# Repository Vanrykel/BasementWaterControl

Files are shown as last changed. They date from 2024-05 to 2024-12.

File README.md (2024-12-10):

# Basement Water Control

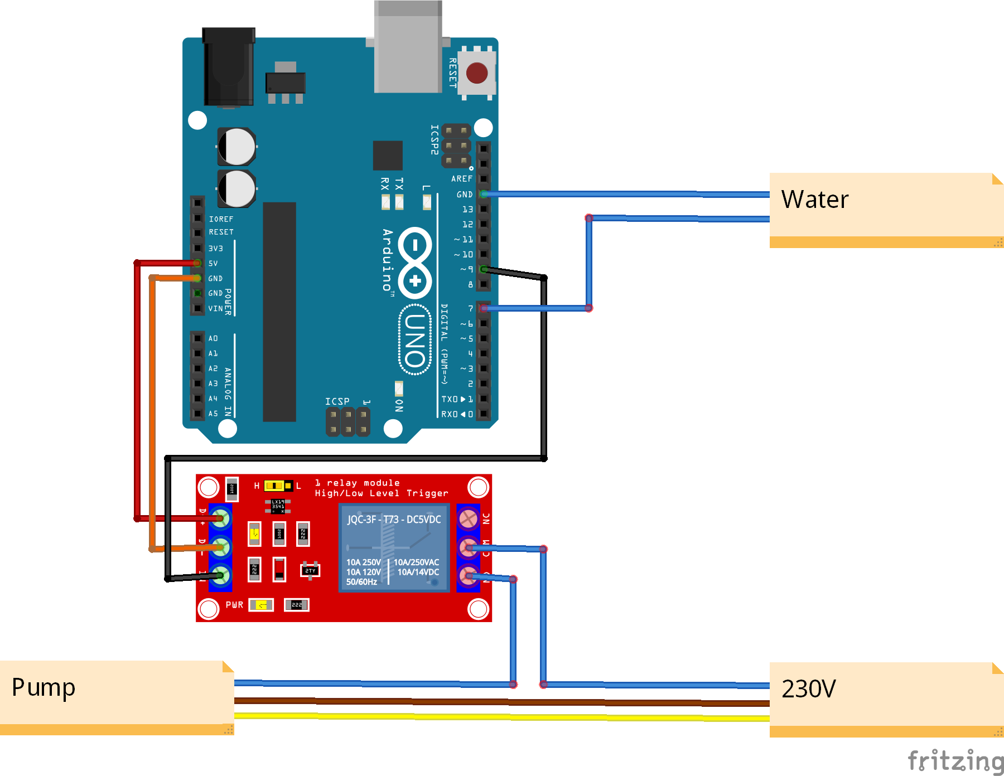
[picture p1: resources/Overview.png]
Overview


## About the project

The basement was consistently flooded with groundwater. To address this issue, a hole has been made in the floor to collect the water, which is then pumped out using a submersible pump. However, due to the shallow depth of the hole, the pump's float switch cannot function effectively. To address this issue, an Arduino is used to detect when the hole in the floor is filled with water. Upon detection, the Arduino will activate a relay to power the submersible pump. The float switch of the pump will be fixed to ensure continuous operation.

**Sequence of operation**

1. Position two loose wires at the upper detection level.

1. Connect the submersible pump to the outlet linked to the relay.
2. Plug in the USB cable of the Arduino.
3. The Arduino awaits water detection (short-circuit pins from step 1).
4. Upon continuous water detection for more than 5 seconds (debounce), activate relay
5. The pump is activated for 10 seconds.

## Materials and methods

- Kärcher SP 9 Flat
- Arduino
- Jumper wires
- Relay board TC-9072472
- Extension cable
- 1 Core Electrical Cable, 0.75 mm

## Results

Different configurations were tested. It all started with a time-based design, but a DIY sensor was quickly added to the project. The DIY sensor was nothing more than two wires running to the detection level of the water hole. One wire was connected to ground and the other to a digital input. The digital input was pulled up to 5V with an external resistor to prevent floating values. Next, I researched using internal pull-up resistors on the Arduino with success. When extending the sensing wires with Wago clamps and 1.5mm wire, the detection of water was not always guaranteed.

Replacing the wires with smaller diameter ones was not an option because the resistance would increase from input to ground. Lowering the pull-up resistor was considered because the internal resistance of the Arduino Uno seems to be 20k-50k ohms. Unfortunately, this did not succeed. Next, the Wago clamps were removed because they could also add to the resistance from input to ground. Therefore, two 0.75mm wires were used so they could be plugged directly into the Arduino Uno. This resulted in great success. Unfortunately, switching the Arduino from laptop power to USB adapter power seemed to have a negative effect on the detection process. Up to four different USB adapters were tested, and only one passed the test. We assume that the ground reference was the issue here.

> ### Special notice !
> Check the USB power supply

## Contributing

Contributions are what make the open source community such an amazing place to learn, inspire, and create. Any contributions you make are greatly appreciated. 

Check out our [contributing page](.github/contributing.md) for how to add issues, features and make pull requests.

## People

- **Dieter Vanrykel** - _OWNER_ - [Dieter Vanrykel](https://github.com/Vanrykel)

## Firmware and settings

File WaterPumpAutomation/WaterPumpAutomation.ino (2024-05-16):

// #define DEBUG_SERIAL_OUTPUT   // Uncomment line to enable serial output for debugging

const int waterSensor = 7;    // Pin to detect water
const int relayPin1 = 8;      // Pin for relay Live wire
const int relayPin2 = 9;      // Pin for relay Neutral wire

bool pumpActive = true;

unsigned long startTime = 0;

void setup() {
  pinMode(relayPin1, OUTPUT); // Live wire pin
  pinMode(relayPin2, OUTPUT); // Neutral wire pin

  pinMode(waterSensor, INPUT_PULLUP);
  
  #ifdef DEBUG_SERIAL_OUTPUT
    Serial.begin(9600);       // Start serial communication
    Serial.println("** Started monitoring **");
  #endif
}

void loop() {
  int waterDetected = digitalRead(waterSensor);
  
  if (waterDetected == LOW) {
    
    if (!pumpActive) {
      #ifdef DEBUG_SERIAL_OUTPUT
        Serial.println("Water detected");
      #endif
      startTime = millis();
      pumpActive = true;
    }
    
    if (pumpActive && (millis() - startTime) > 2000) {
      #ifdef DEBUG_SERIAL_OUTPUT
        Serial.println("Pump activated");
      #endif
      // Activate both relays 
      digitalWrite(relayPin1, LOW);
      digitalWrite(relayPin2, LOW);
      delay(10000);                  // Pump 10 seconds
    }     
  } 
  else
  {
    #ifdef DEBUG_SERIAL_OUTPUT
      if (pumpActive)
        Serial.println("No water detected!");
    #endif   

    pumpActive = false;

    // Deactivate both relays
    digitalWrite(relayPin1, HIGH);
    digitalWrite(relayPin2, HIGH);
  }
}

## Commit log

2024-05-16 Activate pump every hour for 2 minutes
2024-05-16 Activate pump on water detection
2024-05-16 added TimerOn-Delay
2024-12-10 added Fritzing
    [KelderPomp.fzz]
